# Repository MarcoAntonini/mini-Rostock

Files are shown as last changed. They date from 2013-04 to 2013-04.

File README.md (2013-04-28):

mini-Rostock
============

The Rostock mini is a delta 3D printer based on the modified design of the original Rostock created by Johann.
The printer is designed to have a smaller build volume allowing for a smaller, more compact, portable, and desktop friendly version of the delta RepRap design.

This repository is a fork of the original version designed by [Brian Evans](http://www.thingiverse.com/bwevans) with some improvements.

Changes from the orignal project:

* Update carriage,idler_end,platform to accomodate Traxxas 5347 u-joints (According to the latest changes from [Luke](http://www.thingiverse.com/thing:51288) )
* Enlarged frame for the MK1 hot-bed (greater print area)
* Update Extruder with MakerGear Bowden Filament drive

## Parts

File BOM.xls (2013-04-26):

Bill of Materials for Rostock Mini | Suppllier | Quantity | Price | Done
Printed Parts
Motor end |  | 3 |  | OK
Idler end |  | 3
Carriage |  | 3
U-joints |  | 12
Jaws (or Rods qty6) |  | 12
Platform |  | 1
Hotend mount |  | 1
Fan mount |  | 1
Extruder |  | 1
Laser Cut Parts
Lower frame - 6mm acrylic | Formulor GmbH | 1
Upper frame - 6mm acrylic | Formulor GmbH | 1 | €0.00
Printbed insulator - 1/8" cork (3mm) | vorhanden | 1
NEMA17 gaskets - 1/8" cork (3mm) | vorhanden | 3
Hotend groovemount 5mm Plywood | Modellsprot Schweighofer GmbH | 1 | €0.00
Electro-mechanical
NEMA17s - 4.7kg-cm or more | ReprapWorld | 3
NEMA Stepper with Gear 5.18:1 | RobotItaly | 1 | €0.00
608ZZ ball bearings | ReprapWorld | 6
LM8UU linear bearings | ReprapWorld | 6
36tooth GT2 timing pulley - 40 tooth will also work | Stock Driver Products/Sterling Instrument | 3
GT2 timing belt - 2.0mm pitch 976 mm or to configuration | Stock Driver Products/Sterling Instrument | 3 | €0.00
Subminiature switch - Omron SS-5 or similar no lever | Technik-Welt Farnell | 3
Kabelbinder | Technik-Welt Farnell | 100 | €0.00
Sanguinololu controller qt1 - or similar Megatronics v 1.0 | ReprapWorld | 1
6x6" heated printbed | QU-BD 3D Printer CNC Mill Store | 1 | €0.00
MakerGear groovemount hotend | MakerGear | 1
M2 Extrufer Drive Gear | MakerGear or sdp/si, pn# S10T08M020S0508 | 1 | €0.00
40mm cooling fan | ReprapWorld | 1 | €0.00
N-channel MOSFET - IRF540 or similar |  | 1
Power Supply 12V 30A 360W | Well Auction Ltd. | 1 | €0.00
Cable Cable Car Connector 4 pin | drauelectronic | 1 | €0.00
Crimp Plugs, Nylon Spacers 3 mm | WE Elektronik & Computer | 1 | €0.00
Hardware
M2.5x10 | Gedex-Service | 6
M3x10 - flathead | Gedex-Service | 7
M3x12 | Gedex-Service | 30
M3x14 | Gedex-Service | 50
M3x16 | Gedex-Service | 12
M3 fender washer | Gedex-Service | 30
M3 washer | Gedex-Service | 40
M3 nuts | Gedex-Service | 56
M4x16 | Gedex-Service | 20
M4 washer | Gedex-Service | 20
M4 nuts | Gedex-Service | 4
M8x30 | Gedex-Service | 3
M8 washer | Gedex-Service | 6
M8 nuts | Gedex-Service | 3 | €0.00
M3x30 | Modellbau Werkstatt | 30 | €0.00
Traxxas 5347 u-joints | Modellbau Lindinger | 12 | €0.00
8mm precision ground rod - 492 mm length or as configured | CNCShop.at | 6 | €0.00
0.188" OD rigid carbon fiber tube - 166 mm length or as configured | Conrad | 6
Cable Support | Conrad | 2 | €0.00
6x6" 3/16" thick borosilicate glass 152,4 x 152,4 mm 3 to 4,75 mm thick | Glas Gasser GmbH | 1 | €0.00
 |  |  | €0.00

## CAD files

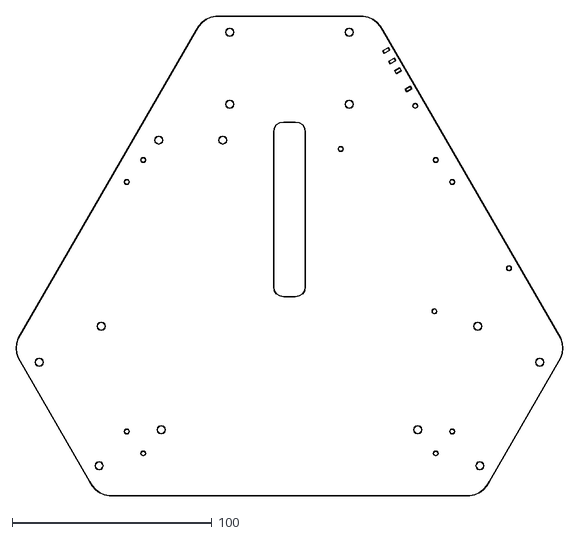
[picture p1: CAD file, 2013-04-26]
DXF/lower_frame.dxf
273.6 x 240.1

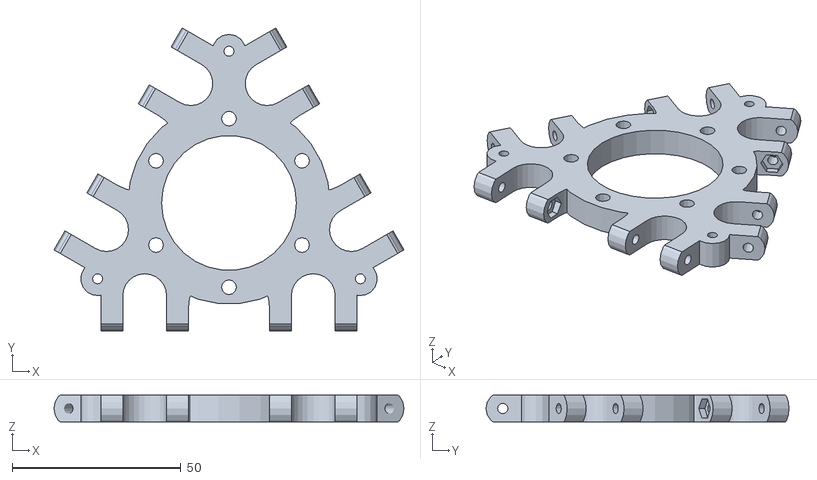
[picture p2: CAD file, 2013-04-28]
STL/platform.stl
103.8 x 89.9 x 8.00

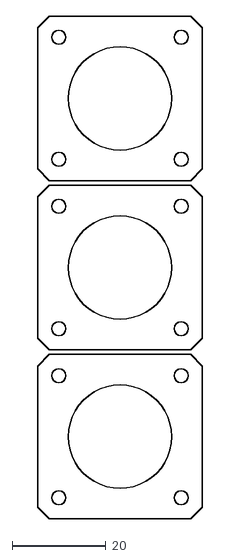
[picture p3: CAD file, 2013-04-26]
DXF/nema14_gasket.dxf
35.0 x 107.0

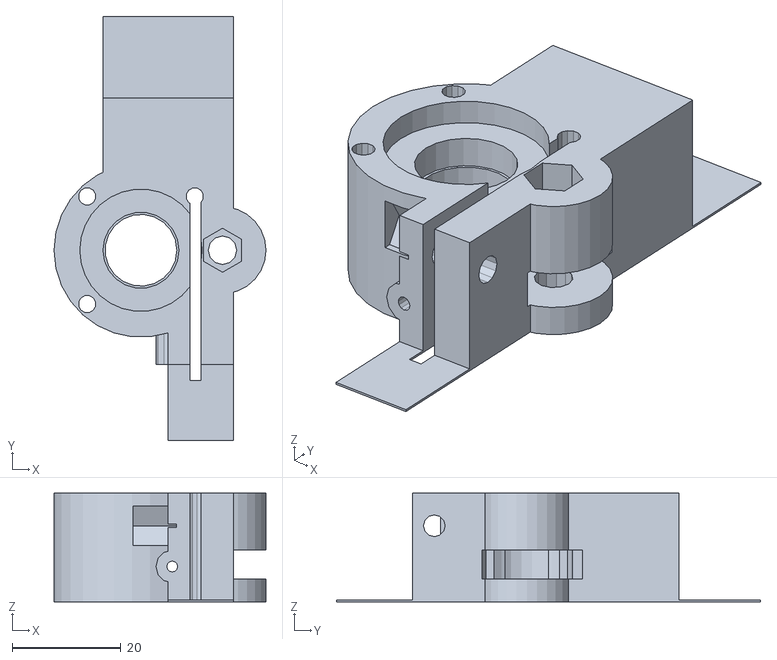
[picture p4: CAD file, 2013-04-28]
STL/filament drive v3.stl
39.0 x 78.0 x 20.0

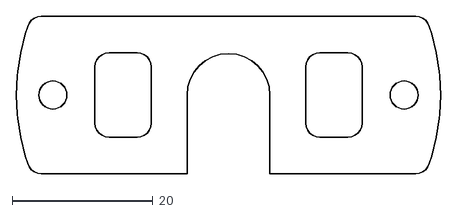
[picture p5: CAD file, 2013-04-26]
DXF/hotend_groovemount.dxf
60.4 x 22.4

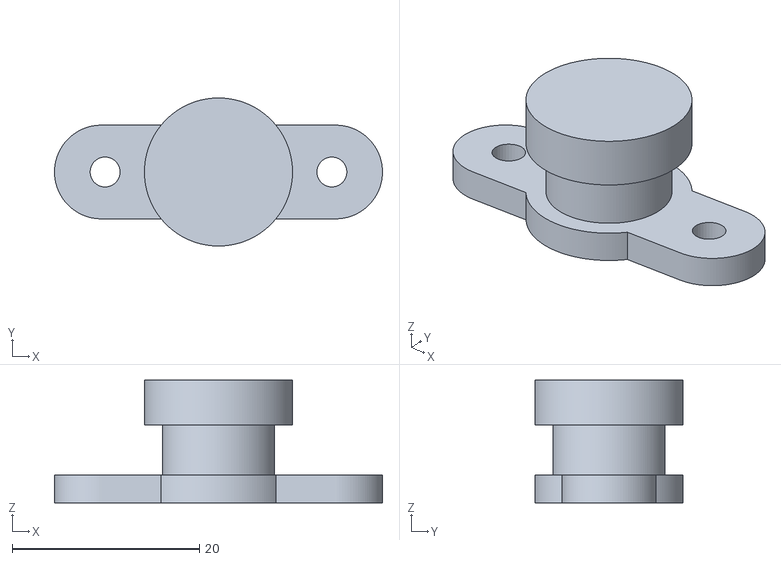
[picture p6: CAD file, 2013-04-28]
STL/bowden_connector.stl
35.0 x 15.8 x 13.1

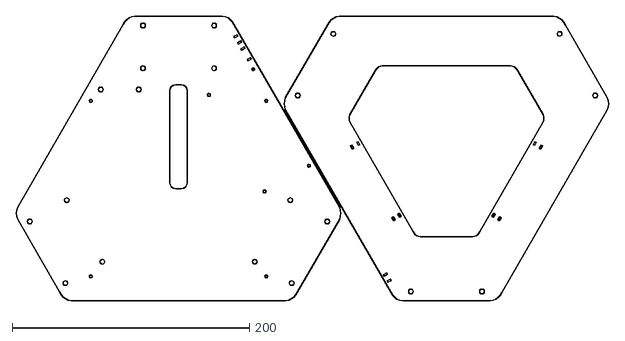
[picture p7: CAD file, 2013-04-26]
DXF/frame.dxf
499.6 x 240.2

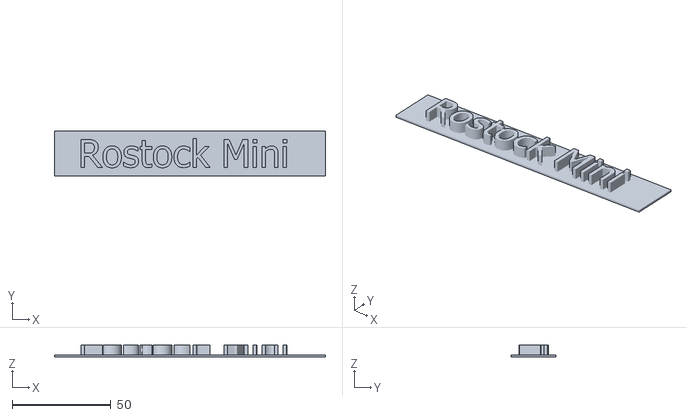
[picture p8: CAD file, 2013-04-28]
STL/nameplate.stl
137.0 x 23.0 x 6.00

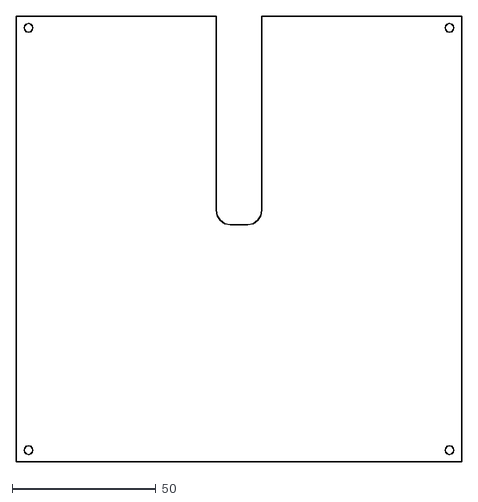
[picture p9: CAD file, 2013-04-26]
DXF/bed_gasket.dxf
155.0 x 155.0

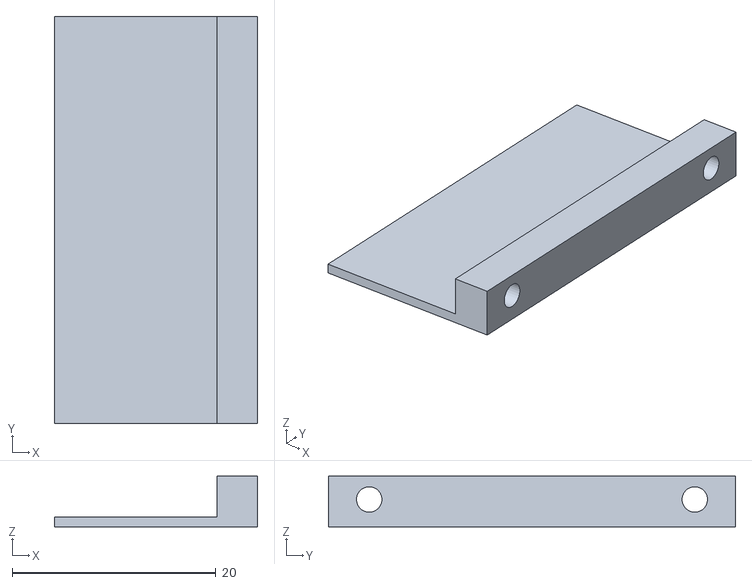
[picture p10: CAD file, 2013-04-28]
STL/Controller_Fan_halter.stl
20.0 x 40.0 x 5.00

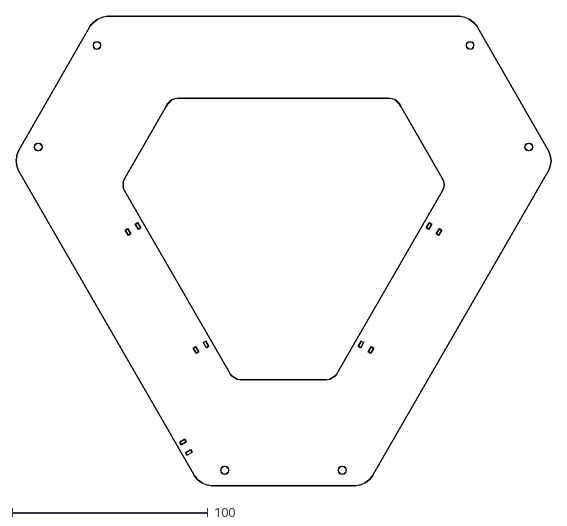
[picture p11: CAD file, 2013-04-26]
DXF/upper_frame.dxf
273.6 x 240.1

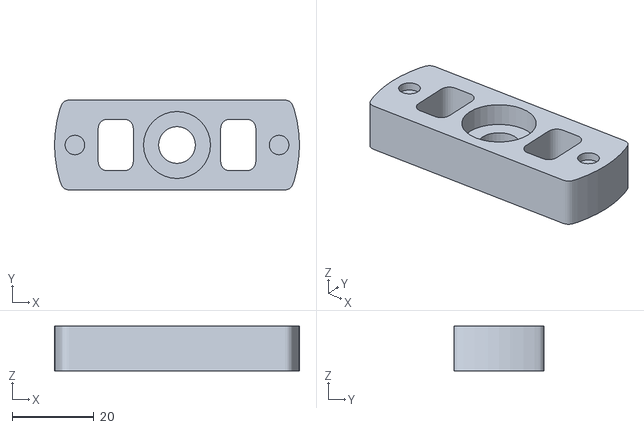
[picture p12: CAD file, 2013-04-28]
STL/hotend.stl
60.0 x 22.0 x 11.0

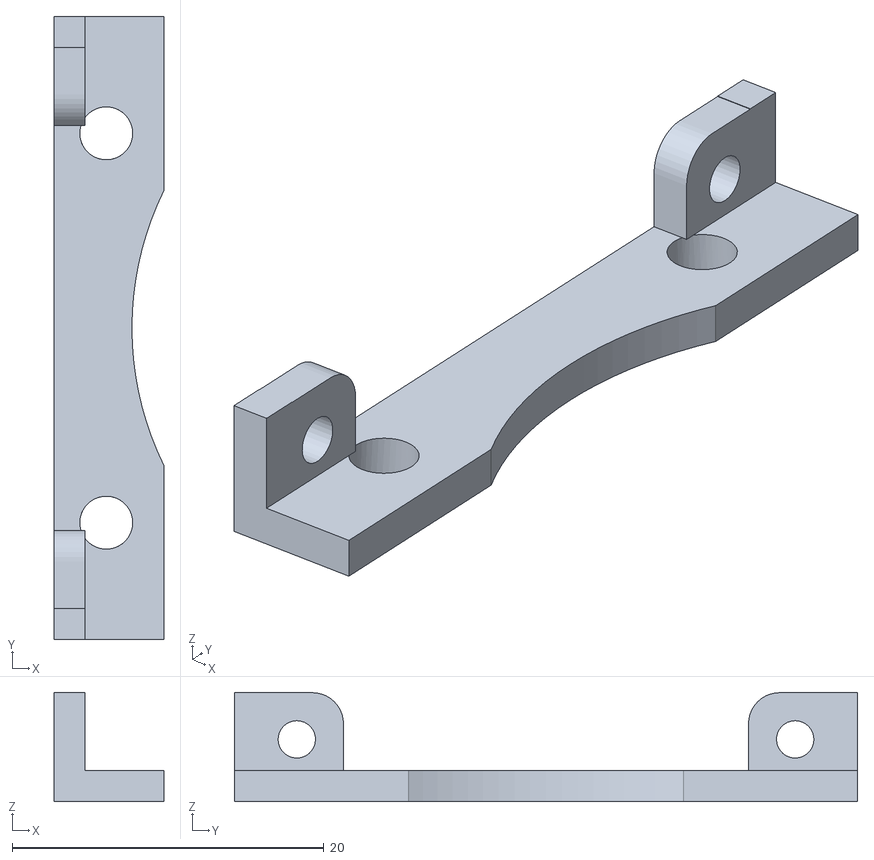
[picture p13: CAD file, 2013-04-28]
STL/nozzle_fan_mount.stl
7.05 x 40.0 x 7.02

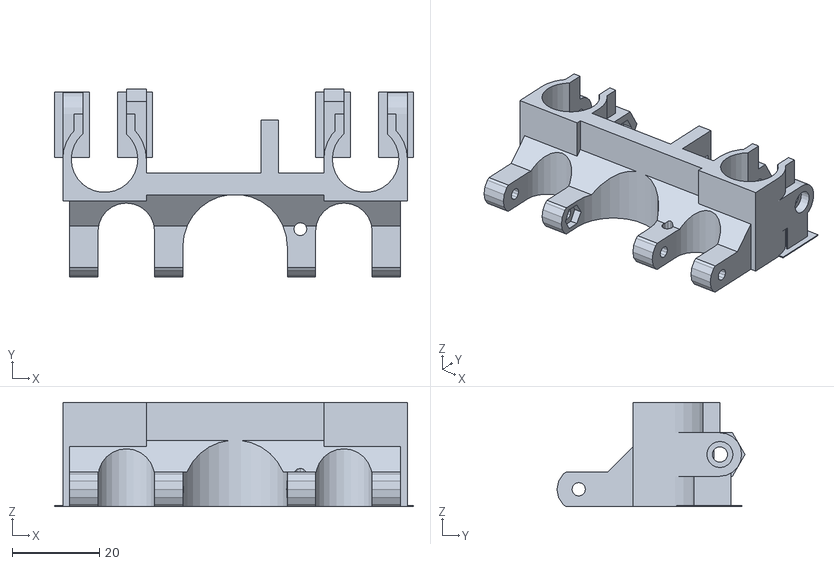
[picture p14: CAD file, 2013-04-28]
STL/carriage-slim_holder.stl
82.5 x 43.2 x 24.0

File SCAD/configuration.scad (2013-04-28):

motor_end_height=44;
idler_end_height=28;
carriage_height=24;
platform_thickness=8;

sanguinololu=true;					// places mounting holes for the Sanguinololu controller
carbon_rods=true;					// turns on option for carbon diagonal rods just for looks!

frame_thickness=6;   				// 6mm acrylic
pcb_thickness=2;						// used for rendering PCB and approximating build volume

smooth_rod_length=800;  				// determins vertical build height with 508 for 8" 
rod_diameter=8;						// might be interesting to have larger rods
platform_hinge_offset=33;
carriage_hinge_offset=22;

printbed=[214,214];  				// printrbed 6x6 155x155-  210,210 for prusa 8x8 platform
printbed_screw_spacing=[209,209]; 	// sets screw spacing for heated bed default: printrbed 146.5,147

tower_radius = printbed[0]*0.9;
rod_length=printbed[0]*1.2;

corner_radius=12;
frame_radius=(tower_radius-rod_diameter/2-corner_radius)/cos(30);

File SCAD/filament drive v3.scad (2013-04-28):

first_layer = 0.3;

difference() {
	
	union() {
		//main cylinder
		translate([16,20,21]) rotate([90,0,0]) cylinder(h=20, r=16);//cube([44, 20, 42]);
		
		//bearing mount
		translate([31,20,21]) rotate([90,0,0]) cylinder (h=20, r=8);
		
		//V3 Mount
		translate([9,0,-7]) cube([24, 20, 22]);
		translate([21,first_layer/2,-11]) rotate([90,0,0]) cube([24, 22, first_layer], center=true);
		translate([27,first_layer/2,45]) rotate([90,0,0]) cube([12, 22, first_layer], center=true);
		
		//filament support
		translate([21.75,6.5,34]) rotate([0,0,0]) cylinder (h=8, r=3, $fn=12);
		
		//groovemount supports
//		translate([33,6.5,-7]) rotate([0,0,0]) cylinder (h=16, r=5, $fn=12);
//		translate([9,6.5,-7]) rotate([0,0,0]) cylinder (h=16, r=5, $fn=12);
		
		//clamp
		translate([21,0,28]) cube([12, 20, 14]);
	}
	
	//pulley opening
	translate([16,21,21]) rotate([90,0,0]){
		cylinder (h=22, r=6.6);
		
		rotate([0,0,45]) {
		//translate([14,0,0]) cylinder(h=22, r=1.6, $fn=12);
		translate([0,14,0]) cylinder(h=22, r=1.6, $fn=12);
		translate([-14,0,0]) cylinder(h=22, r=1.6, $fn=12);
		translate([0,-14,0]) cylinder(h=22, r=1.6, $fn=12);
		}
	}
	
	//gearhead indentation
	translate([16,20.01,21]) rotate([90,0,0]) cylinder (h=3.35, r=11.25);

	//pulley hub indentation
	translate([16,20-2,21]) rotate([90,0,0]) cylinder (h=5.6, r=7);
	
	//bearing screws
	translate([31,21,21]) rotate([90,0,0]) cylinder (h=22, r=2.625, $fn=12); //precision m5
	//translate([31,21,21]) rotate([90,0,0]) cylinder (h=22, r=2.6, $fn=12); //regular M5 screw
	translate([31,22,21]) rotate([90,30,0]) cylinder (h=8.01, r=8.1/2, $fn=6); //M4
	//#translate([31,22,21]) rotate([90,30,0]) cylinder (h=8.01, r=4.7, $fn=6); //M5
	
	//bearing
	translate([31,9.5,21]) rotate([90,0,0]) cylinder (h=5.25, r=8.5);
	translate([31,9.5-5.25,21-8.25-2]) cube([20, 5.25, 18.5]);
	//opening between bearing and pulley
	translate([20,9.5-5.25,21-8.25+3.25+1]) cube([10, 5.25, 8]);

	//filament path chamfer
	translate([21.75,6.5,15]) rotate([0,0,0]) cylinder (h=2, r1=1, r2=1.5, $fn=12);		
	
	//filament path
	#translate([21.75,6.5,-10]) rotate([0,0,0]) cylinder (h=60, r=1, $fn=12); 
	
	//V3 Mount
//	translate([21.75,6.5,-2]) rotate([0,0,0]) cylinder (h=5, r=8.25);
	translate([21.75,6.5,-7]) rotate([0,0,0]) cylinder (h=8, r=4.5);
//	translate([21.75-8,6.5-8,-2]) cube([16, 8, 5]);
//	translate([21.75-6,6.5-7,-7]) cube([12, 7, 5]);
//	translate([21.75,6.5,3.5]) rotate([90,0,0]) cylinder (h=10, r=1,  $fn=12);
	
	//groovemount supports
//	translate([33,6.5,-8]) rotate([0,0,0]) cylinder (h=20, r=1.6, $fn=12);
//	translate([33,6.5,7]) rotate([0,0,0]) cylinder (h=3, r=3.5, $fn=6);

//	translate([9,6.5,-8]) rotate([0,0,0]) cylinder (h=20, r=1.6, $fn=12);
//	translate([9,6.5,7]) rotate([0,0,0]) cylinder (h=3, r=3.5, $fn=6);
//	translate([3,3,7]) cube([8, 7, 3]);
	
	//clamp slit
	translate([25,-1,10]) cube([2, 22, 35]);
	//clamp nut
	translate([14.5,14,38]) rotate([0,90,0]) cylinder (h=8, r=4.2, $fn=6);
	//clamp screw hole
	translate([15,14,38]) rotate([0,90,0]) cylinder (h=20, r=2, $fn=12);
	
	
}

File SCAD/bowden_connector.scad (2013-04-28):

$fn = 0;
$fa = 0.01;
// use $fs to control the number of facets globally
// fine ~ 0.1 coarse ~ 1.0
$fs = 0.3;
diameter = 9.5; // diameter for cutting thread
height =8; // hight of thread

module groovemount() {
	translate([-25/2,-10/2,0]) cube ([25, 10, 3]);
	translate([-25/2,0,0]) cylinder(h=3, r=10/2);
	translate([25/2,0,0]) cylinder(h=3, r=10/2);
	cylinder (h=4.8+5.3+3, r=12/2);
	translate([0,0,3+5.3]) cylinder (h=4.8, r=15.8/2);
	cylinder (h=4.8+5.3+3, r=12/2);
	cylinder (h=3, r=15.8/2);
}
difference() {
	groovemount();
	translate([-12.1,0]) cylinder(h=3, r=3.2/2);
	translate([12.1,0]) cylinder(h=3, r=3.2/2);
	cylinder (h=height, r=diameter/2);
	cylinder (h=4.8+5.3+3, r1=1);
}

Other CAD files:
STL/M2 Extruder Motor Mount.stl
STL/idler_end.stl
STL/jawsx6.stl
STL/idler_end_1deg.stl
SCAD/hotend.scad
SCAD/bearing.scad
SCAD/bed_clip.scad
SCAD/belt.scad
SCAD/bracket.scad
SCAD/carriage-slim_holder.scad
SCAD/carriage.scad
SCAD/carriage_old.scad
SCAD/extruder.scad
SCAD/fan_mount.scad
SCAD/flange.scad
SCAD/frame.scad
SCAD/hotend_old.scad
SCAD/idler_end.scad
SCAD/idler_end_old.scad
SCAD/jaws.scad
SCAD/joint.scad
SCAD/lm8uu-holder-slim_v1-1.scad
SCAD/motor_end.scad
SCAD/mounting_screws.scad
SCAD/nema.scad
SCAD/nema14gasket.scad
SCAD/penholder.scad
SCAD/platform.scad
SCAD/platform_old.scad
SCAD/pulley.scad
SCAD/rod.scad
SCAD/rostock_mini.scad
STL/bed_clip.stl
STL/carriage.stl
STL/extruder.stl
STL/extruder_bracket.stl
STL/extruder_idler.stl
STL/fan_mount.stl
STL/jointx12.stl
STL/motor_end.stl
STL/old_original_stl/carriage_old.stl
STL/old_original_stl/hotend_old.stl
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

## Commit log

2013-04-26 Init Fork from http://www.thingiverse.com/thing:32850
    [bearing.scad, bed_clip.scad, bed_clip.stl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]
2013-04-26 Added BOM
    [BOM.xls, configuration.scad]
2013-04-28 modified configuration to accommodate MK1 hotbed (124x124mm)
    [configuration.scad]
2013-04-28 Updated parts according to the latest changes from Luke http://www.thingiverse.com/thing:51288
    [Controller_Fan_halter.stl, M2 Extruder Motor Mount.stl, bowden_connector.scad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]
